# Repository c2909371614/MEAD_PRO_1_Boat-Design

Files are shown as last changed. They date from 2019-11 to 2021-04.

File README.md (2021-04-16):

# MEAD_PRO_1_Boat-Design

机器人学院的MEAD 项目--小船项目分享

<<<<<<< HEAD
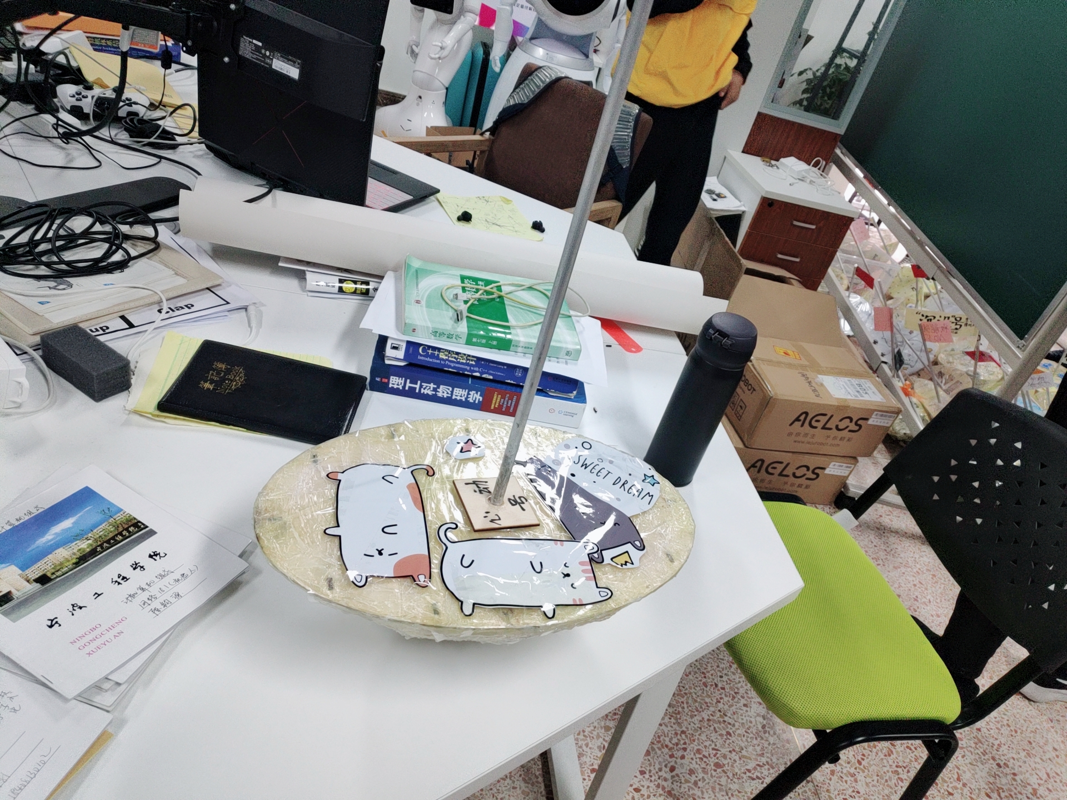
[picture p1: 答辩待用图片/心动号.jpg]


=======

>>>>>>> a22fceb2be759056432b4c75dd355906650863ec
<center> fig 1. 心动号 </center>
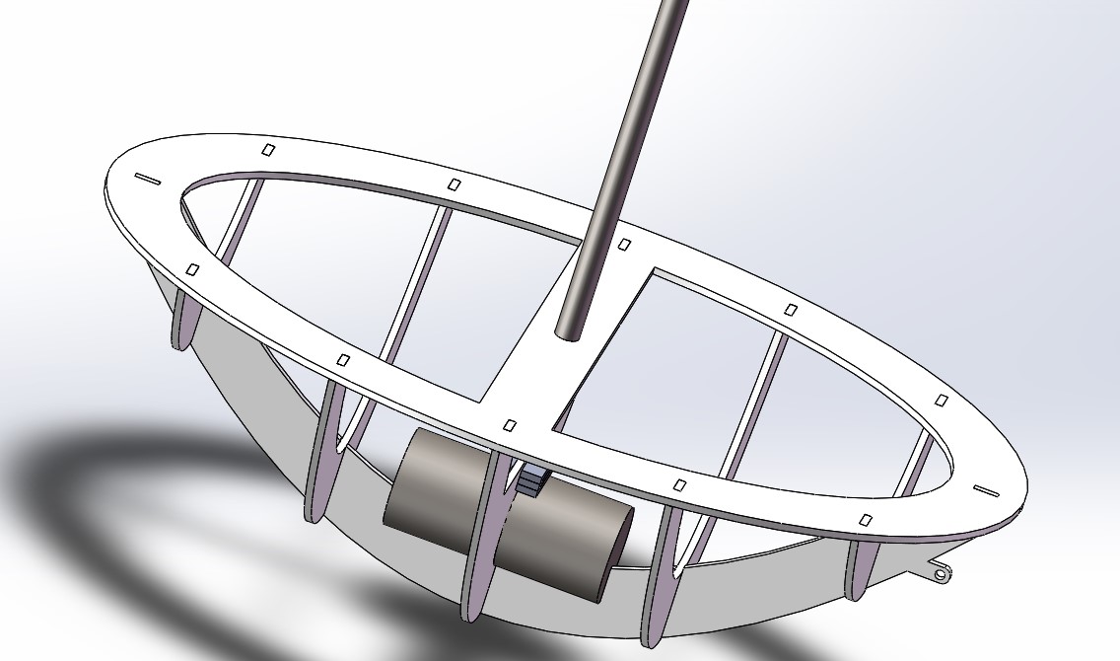
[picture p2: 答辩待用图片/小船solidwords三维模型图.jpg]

<center> fig 2. 小船solidwords三维模型图 </center>
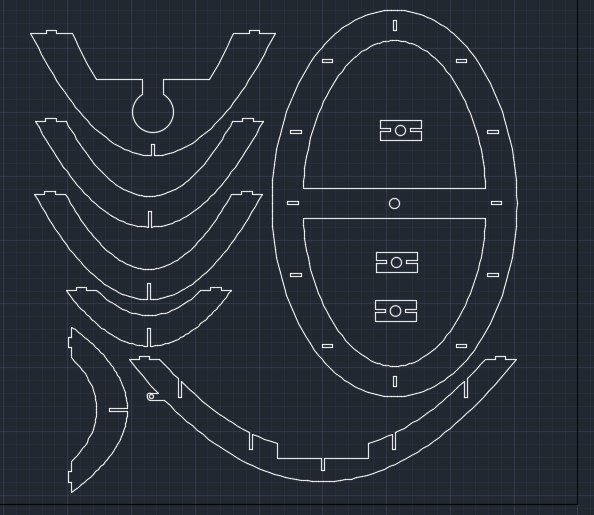
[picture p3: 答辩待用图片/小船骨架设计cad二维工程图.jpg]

<center> fig 3. 小船骨架设计cad二维工程图 </center>

### 一、MADE项目任务书-- 船只设计项目

		Welcome to the MADE project!!! Here, MADE stands for Mathematical Analysis and Design for Engineering. This is a project-based course, which aims at improving the participators’ understanding of mathematics knowledge and engineering analysis. MADE should be able to help the students to develop a thinking mode of applying theoretical analysis and quantitative calculation, and truly understand the role of mathematics in engineering projects. 

		欢迎来到MADE项目课程。在这里，MADE代表着“用于工程的数学分析和设计”。MADE项目力求以实际应用的案例加深参与者对数学知识与分析方法的理解，并逐步建立在工程问题中采用理论分析进行定量计算的思维模式，真正掌握在实际的工程设计中应用数学知识的方法。

		MADE course is supposed to be challenging, comprehensive, and integrate knowledge of various subjects. But please be assured that the task is feasible, and we look forward to seeing you confidently say, ”Yes, I MADE it!!”

		MADE课程在设计时，就力求做到具有挑战性，全面性，并整合各种科目的知识。但请放心，这项任务是可行的。我们期待看到你自信地说：“Yes， I MADE it！”

**MADE Project 1: Boat Design**

此项目要求你设计一艘船，并满足一定的设计要求。要达到这些要求，你必须要完成制作、测试、研究和计算等多项工作。我们希望通过这项课程中对设计与分析等不同方面的练习，你可以在未来更有信心的面对各项技术工作。

要完成这个项目，你需要各类工作，制作各类零件，并完成你的设计工作。最后，你要展示你的作品，并通过答辩。

**项目对你的预期：**

1. 你应该对船舶设计过程进行背景研究。为此你可能需要在互联网上花费相当多的时间。我们建议你整理出一个造船业的术语列表，并且要确保自己不仅理解造船业中的why，还要了解其中的how。这本身是一个巨大的话题。因此，你可能不会成为专家，但应该熟悉关键的思路。你需要理解的术语包括但不限于：倾斜heel，流线trim，船宽beam，稳定消失角AVS，水下表面积，浮力，位移等

2. 你应该做一些估算，以指导和验证你更详细的设计和分析工作。任何你做出的决定，你都应该能够通过一个快速的计算或论证进行支撑。这个计算或论证至少能够表明你的决定在正确的范围内。不要忘记在正式开始建造你的船模之前检查你的最终设计。设计方案是否准确？它看起来是否稳定？

3. 您应该进行详细的分析以支持您的设计选择，并验证您的测量结果。您应该依靠计算支持你的设计方案。我们要超越猜测和检查的方式，需要使用图表，研究不同选项等。

4. 你要建造一艘船，并将其性能与你的理论分析预测的性能进行比较。

**我们期望你能制造出：**

1. 首先，您需要提供一艘船模，并满足下面指定的设计要求。在项目的最后一天，把这艘船带到课堂上。请注意，在此之前绝对不允许对你的船模进行测试

2. 你需要提供可用于分析给定船舶设计的代码。代码规范细节在文件后续中有说明。

3. 您需要提供一份设计报告，通过计算和测量来对你所做的设计选择进行总结和证明。

4. 最后，您需要提供一份修改后的设计报告以及一封给老师的反馈信，说明在答辩以后，为响应教师建议所做的修改。

**最后要达成的目标**

1. 我们将集体做船的测试。想象一个产品展示日

2. 你的团队将与教师一起坐下来审核您的设计报告。教师将为您提供有关如何改进设计报告的具体反馈等。您将有三天时间修改报告以回应这些建议，并在一页信总结相关的改变。

**船只的设计要求**

您将使用激光切割的硬质板框架设计和制造船只，并且利用所提供的材料构件外壳。

**制造要求**

1. 你只能使用一块***600mmX450mm***的一块硬质板；

2. 必须使用公式驱动的CAD模型创建船只，

3. 船必须接受最小质量为700，最大质量为1000克的货物。在将货物固定在船上之前，应该预先接受检查和批准。

4. 船必须是不含**舭龙骨**的单体船设计（即不得使用外延龙骨板或双船体）

5. 船必须包括桅杆。桅杆将是一个0.5米长，直径***10mm***的铝棒。桅杆的整个长度必须垂直延伸在船底之上。（不得延伸到船底之外）

6. 应将孔眼按照所需的拖曳点连接到船体上，以便进行速度测试。

**性能要求**

请记住，在最后一次挑战之前**不得**进行测试。您应该能够根据计算，知道您的船能否符合以下的各项要求。

1. 当船满载时，必须能够漂浮起来;

2. 当船满载漂浮时，船的甲板应平行于水面;

3. 满载船的消失稳定角（AVS）应该是135度，允许有±10度误差;

4. 船应具有至少0.2 N-m的最大恢复力矩；

5. 船体应尽可能利于快速行进。这一点将使用拉力测试来确定：通过连接在螺旋孔眼处的水平线施加0.1牛顿的恒定力来进行。

**专业性要求**

1. 船模的外观应该很专业；

2. 应该用你们的队名适当装饰你的船模；

3. 制造的船应与报告中的船模设计相同。也就是说，不允许测试前临时修改！！

**代码**

你要创建一段程序代码，用于计算给定船舶设计的重要参数。本节内容概述了对代码的要求。请注意，这些要求的编写方式意在引导你逐步增加各项内容。

你的代码应该包含以下内容，

1. 船体形状的数学函数表示。可以使用符号数学或代码来完成，这会创建一组离散的点，来根据函数形式定义曲面。如果您正在进行二维近似，那么您应该能够在答辩中说明此近似的有效性，包括在计算中如何考虑第三个维度； 

2. 船体形状的可视化，以及来自所有三个方向（纵向，横向和吃水线）的切面的显示

3. 计算给定载荷时的位移，和对于给定载荷和船体倾角的相应吃水线；

4. 为你的船体设计计算质心和浮心，以及这些位置如何随着船体倾角的变化而变化;

5. 在特定负载配置下，你的船体设计方案中，绘制复原力矩作为船体倾斜角函数的曲线图。你应该检查这些结果，确保它们与计算出的质心和浮心位置保持互相吻合。

### 二、我完成了什么

根据小船设计要求（见小船设计项目任务书文件）

1、求出小船底部曲面方程及船高

2、求出龙骨方程、截面方程及甲板方程

3、求出重心及小船向x轴倾斜135°（船体封闭）时的浮心及复原力矩

4、求出吃水线

5、画数量关系图

5.1画出重物质量与吃水线关系的曲线图

5.2画出船长、宽、高分别与复原力矩关系的曲线图

5.3 画出重物质量与重心关系的曲线图（曲线图的纵横坐标表示重心坐标，曲线上的点的大小表示质量）

### 三、解决方案概要

> 		针对如何使用一块***600mm x500mm***的木板制造一艘在承载一定质量的重物的情况下能够平稳的漂浮起来切具有稳定消失角(AVS)的方案进行了研究。通过数学曲面公式来简单的表示船体的曲面，通过曲面积分来计算船体体积、吃水线性、船体的浮心和重心，确定浮心、重心之后计算出倾斜一定角度时的复原力矩。通过使倾斜一定角度时船体重心在浮力方向和船体中心线的交点上来确定AVS(135°)。

>  	以小船最低点为坐标原点，垂直垂直向上为Z轴，船头至船尾的连线为Y轴建立直角坐标系以方程为船体底部曲面方程，最终确定A=8.33，B=3.33，计算得船长length为0.379m，宽width为0.240m高height为0.120m，桅杆重心(0,0,0.292)，重物重心(0,0,0.042)，船体重心为(0,0,0.080)。

### 四、详细解答过程请看项目报告书，找不到自己想要的请留言（by a new issue)

### RESULT



<center>图3 船体倾斜135°复原力矩图

已知$COM(0,0,z_m)$，$COB(x_b,0,z_b)$

浮力$F_浮=<tan\theta,0,-1>\lambda$，其中$\lambda=\frac{G_{all}}{tan^2\theta+1}$

复原力臂$r=COM-COB=<0,0,z_m-z_b>$

复原力矩$M_s=r\times F_浮=0$

### 4.吃水线



<center>图4 水平吃水线

已知船体总重量为$m_{all}$，有$m_{all}=\rho g_水 v_排$

吃水线方程为$z=h$

有
$$
\begin{align}v_排=&\iiint_E{dV}\qquad E = \{(x,\ y, \ z) | x_{Mid}\leq x\leq width, \ y_0\leq y \leq0, 0 \leq z \leq z_0 \}\tag{4}\\v_排=&\int_{xMid}^{x_1}\int_{0}^{y_0}\int_{Ax^2+Bx^2}^{h}{xdzdydx}\tag{5}\end{align}
$$

###

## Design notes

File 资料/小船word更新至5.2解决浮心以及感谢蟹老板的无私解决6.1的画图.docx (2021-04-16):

以小船最低点为坐标原点，垂直向上为Z轴，船头至船尾的连线为Y轴建立直角坐标系假设船体底部曲面方程为，船高为，桅杆长度0.5m，质量0.1kg，重物的底面半径0.02m，质量1kg，材料面密度为0.1458kg/m²

求

1、 龙骨方程

x取0，得到z=By²,即为龙骨方程。

2、 任意截面方程

设截面所在平面为ax+by+cz+d=0①

则任意截面方程为①与相交部分，即

（a,b,c,d为任意常数）

3、 甲板方程

甲板面平行于xoy平面，所以令曲面方程中的z=H即可。即

4、假设A=17656，B=14.8，H=0.2

4.1求吃水线深度

先求m总=m船+m甲板+m重物+m桅杆

已知桅杆的质量为0.1kg，重物的质量为1kg

所以m总=m船+m甲板+1.1

已知船的面密度，求得船的表面积即可求得船的总重。所以

由于投影面为，对称性好。可以将积分转化为第一象限积分的四倍。即

所以船体的总表面积为

使用matlab的quad2d函数求解，得到结果为 0.113379476543658m³

再用ρV=m求得m船体= 0.016530727680065kg

最终求得m总=1.116530727680065kg

再使用m=ρ水V排；ρ水=1000kg/m³；求得V排=m*10⁻³,单位m³。

因为甲板平行于水面，所以设吃水线高度为H对浸入水内船体进行体积积分，即求得V排。

通过二分法迭代求H，最终求得H=0.120879583074898m，即吃水线深度。

4.2求重心

根据方程可以知道船体有良好的对称性，关于x轴y轴均对称，即船体的重心的x坐标和y坐标均为0。仅需求z坐标即可。

使用matlab的quad2d函数求解，得到结果为0.003030405142533m。

已知三点P（0，0，0.003030405142533），Q（x1,y1,z1），R(x2,y2,z2)

(P为桅杆重心，Q为重物重心)

三点对应质量为m0=0.016530727680065kg,m1=0.1kg,m2=1kg。所以质心坐标的xyz坐标如下：

质心坐标为，单位均为m。

5.1 将小船向 x 轴倾斜 140°求出吃水线所在平面的方程

方法①：坐标系转换（把船转过去）

方法②：把水转过来。（以船自身为坐标系）

位置是相对的，既然将小船转140°入水，组成船-水的相对位置；也可以将水面转过来140°组成水-船的相对位置。既然如此，水面就是一个平面，即z=tan140°x+k,这个k就是关键，利用水下船体体积*水的密度=船的总重可以求出k值，确定该水面方程，以船自身为坐标系的该水面方程即为吃水线方程。

以下将进行对于方法二的求解：

已知船的坐标方程和吃水线方程，求k。k有三个临界点，分别是

①吃水线与原点相交（水漫得最高，ps:排水体积大于总体积一半肯定够了）

排水体积关于z轴分为两部分，右侧的体积为总体积的一半远大于所需排水体积，左侧未算，但是肯定是大于0的。

②吃水线与船的左上点相交(水漫到的关键点，ps:通过计算漫到这点排水体积还不够一点点)

根据z=tan140°x+k与可以求得k=0.151320293728474；然后求吃水线与船的另一侧的交点的x值，使用联立求解可以求得x=x0=0.049897854853113（我是使用二分迭代的方式求得的）；最后使用积分求其排水体积。此处使用船体总体积减去水上体积更容易计算。船体总体积已经算过了，使用第四题中的结果即可。水上体积表达式如下：

积分出来结果为0.001595895710214m³。

再用船体总体积减去其积分结果，求得水下体积为0.001099084023240m³略小于所需排水体积0.001116530727680m³

③吃水线与船中心的最高点相交(水漫到的最低点，ps:通过计算漫到这点排水体积还是不够)

最终计算结果说明：

由①②③可知，k在k1和k2之间，k1即①中的k=0，k2即②中的k=0.151320293728474;

此时k为变量，通过二分迭代，每次计算k时，分别计算水面与船体的交点的x轴坐标，此时的计算函数其实类似与②中的公式，只需要将x0和这两个上下限，改成由随k而变的xmin和xmax，这两个值也可以利用每次二分迭代k的时候，使用二分迭代求得。最终利用②中的积分和船的总体积求得排水体积。此处只给出结果，k=0.150534414731095。

最终那个吃水线方程为z=tan140°x+0.150534414731095。

5.2 将小船向 x 轴倾斜 140°，求浮心及复原力矩

浮心：

已知水下船体关于y轴对称，对称区域也关于y轴对称，所以关于y的奇函数的积分为0。根据浮心定义：浮心就是被排开的流体的重心。所以可以利用重心公式求解。

设其坐标为，已知y0=0。仅需求x0和z0即可。

已知吃水线方程为，k为已知常数（0.150534414731095）。所以可以根据吃水线平面和船体的交线求得两端交点x1，x2，此处由5.1二分迭代求k的过程中已求出，分别为-0.057953430474795和0.049815920068628。然后将积分区域分成三片，左边右边两块和中间一块。三块y的上下限均在之间；左右两块z的上下限分别为H和曲面方程，中间一块z的上下限分别为H和吃水线平面方程；而三块x的范围，以x1，x2分割，左边的在与x1之间，中间的在x1，x2之间，右边的在x2和之间。最终按重心三重积分求结果。以下为公式：

;

关于x：

右边的积分同理可得，只要将上下限换掉即可。

将三者积分相加，除以m得最终浮心的x坐标，约为0.013938450731625，单位m。

关于z：

右边的积分同理可得，只要将上下限换掉即可。

将三者积分相加，除以m得最终浮心的z坐标，约为0.170003799370430，单位m。

复原力矩：

复原力矩

6.1 画出重物质量与吃水线的曲线图

①4.1船的重量公式算出船的总重，再根据V排=总重量

求出对应的吃水线H，再用程序求出每次增重1g对应的吃水线。画图

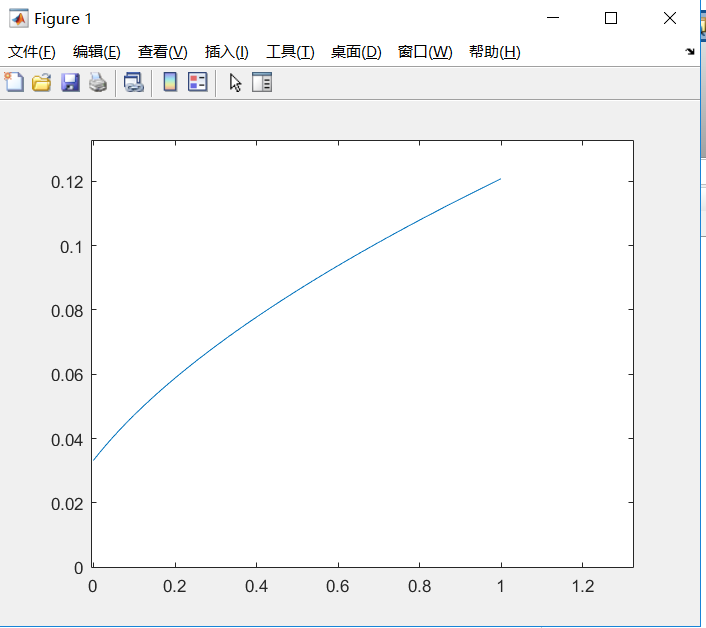
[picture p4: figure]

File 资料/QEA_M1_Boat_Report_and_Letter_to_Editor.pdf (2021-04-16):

# Designing the Steggie

Kyle Combes & Alex Core

Abstract—This report will detail the necessary background information of boat making through mathematical functions, explain specific design decisions and reasoning behind these choices, elaborate on the various calculations involved in this process, and discuss the real world performance of the boat. The performance qualifications of this project were to design a boat that floats in water, has a parallel deck to the surface of the water. The angle of vanishing stability is between 120◦

and 140◦
,
has a maximum computer righting moment of at least

### 0.2 Newton-meters, and is as fast as possible under a

constant force of .1 Newtons. The boat will be made out of hardboard and vinyl, and will contain a mast and eyelet. The project required a understanding of the background and terminology involved to make proper calculations using Mathematica. This use of mathematica was only possible with a understanding of the basics of multivariable calculus and the physics ideas of center of mass, center of buoyancy, and torque. The design was started as simple and was adjusted to the needs of the Mathematica calculations and utilized to find equations that define the boat. These equations were then exported to Solidworks. The parts of the boat were laser cut out of hardboard and then glued together and wrapped and vinyl. The boat was then tested for the above requirements.

I. BACKGROUND AND TERMINOLOGY

To understand the boat, a basic foray into the terminology and ideas behind boats and boat building was necessary. One such area needing exploration was the parts of the boat. The hull is the main body of the ship of the vessel including the bottom, sides, and deck. The bow it the forward part of the hull of the ship or boat it is a necessary proponent to drag. The stern in contrast is the after most part of the hull. The deck is an important part of the design and is the topmost portion of the boat. Where the hull meets the water is the waterline, which is essential to calculations. The buttock is the lines formed at a point of intercepts between the centerline plane and the sheer plane. A section is a division of a boat on a plane. The heel angle is the amount the vessel is tilted from upright. Center of mass (COM) is a point representing the mean position of matter. Physics calculations can be focused on that one point. The center of buoyancy(COB) is the centroid of the submerged part of the boat. This can thought of as the center of mass of the displaced water for simplicity. One facet of this project is the angle of vanishing stability (AVS). The AVS is the heel angle at which the the boat is between capsizing and self righting. It can barely balance due to the center of mass and center of buoyancy being at a equilibrium. The righting moment is the is the restoring force of the torque which is created by the center of mass and center of buoyancy to self right when the heel angle is above the AVS.

II. DESIGN CONSIDERATIONS

A. Units and Conventions
All of our units were in inches and grams, and we used a right-hand, 3D coordinate system with the origin at the center of the bottom of the hull. The x-axis ran port to starboard, with starboard being positive, and divided the boat in half. The y-axis ran lengthwise, also dividing the boat in half, with the bow in the positive direction. The positive z-axis extended skyward. (See Figure 1.)

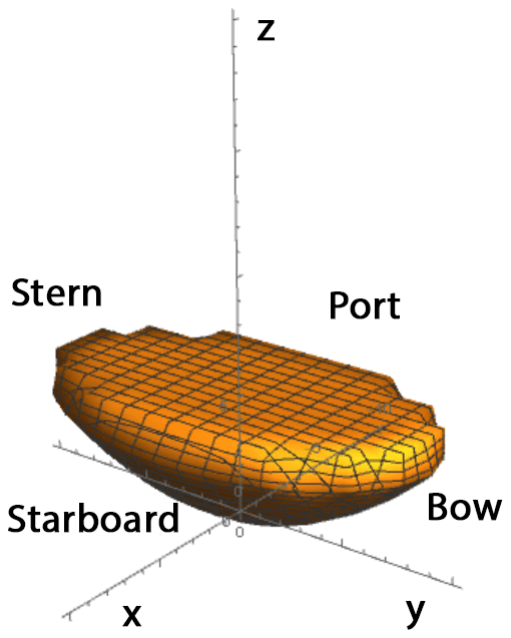
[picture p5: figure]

Fig. 1: Our coordinate system was defined with the x-axis running from port to starboard, the y-axis running lengthwise, and the z-axis extending vertically.

In order to simplify our calculations, we decided to model a rotating waterline rather than a rotating boat. As such, the forces of gravity and buoyancy rotated with the water. θ represented the angle of rotation of the waterline, with positive being a counter-clockwise rotation about the y-axis.

B. Making a Floating Boat
The first step in designing a boat is to make sure it’s going to float. Generally speaking, when an object floats in water, the buoyant force pushing back up on that object is equal and opposite to the force pushing the object down in the water. With a boat, the downward force is the force due to gravity (Figure 2). Therefore, for a buoyant boat:
F~B = −F~Gboat | (1)

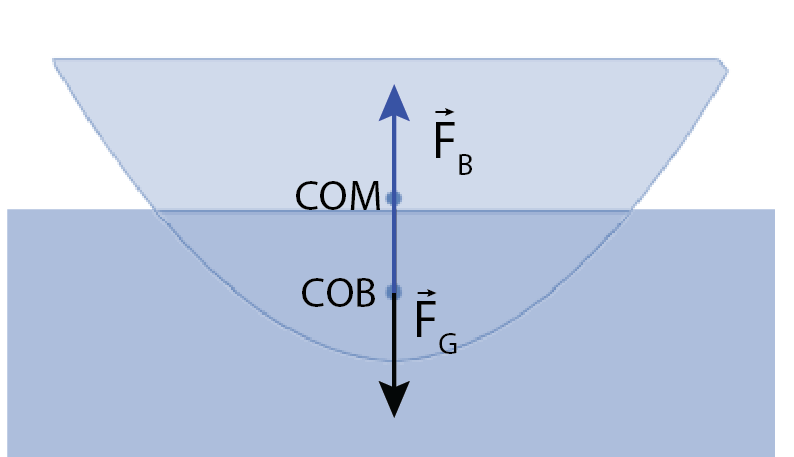
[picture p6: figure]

Fig. 2: When a boat is floating, the buoyant force is equal and opposite the force due to gravity acting on the boat.

Additionally, the buoyant force is equal to the mass of the water displaced multiplied by the acceleration due to gravity.

F~B = mwaterg | (2)

Since the mass of water is equal to its volume times its density, we can also write:

F~B = ρwaterVwater~g | (3)

That means that in order for our boat to float, the boat must have suitable density and displace enough water such that the buoyant force can counteract the force of gravity.

C. Finding the Waterline
The buoyancy concept can be extended to find the waterline on the submerged vessel. If the floating boat has a mass, mboat, then the water it displaces must also have the same mass:
mboat = mwaterdisplaced | (4)

The mass of the boat can be calculated by integrating all of the point masses in the region defined by the boat. Similarly, the mass of the displaced water can be found by taking the volume of the submerged region of the boat (found by integration) and multiplying it by the density of water. (One must remember to take into account the fact that the waterline is rotated when defining the submerged region.) Combining these two concepts allows us to rewrite the above equation as follows:
Z Z

~r∈Boat

ρboatd~r =

Z Z

~r∈Submerged

ρwaterd~r (5)

Solving for the upper bound on the submerged region will give you the waterline.

D. Making it Sit Flat
In order to meet the second requirement, it is necessary to design the boat such that the COM and COB are aligned along the x- and y-axes when the plane of the deck is parallel to the plane of the water. Otherwise, a torque will result about the COM, as illustrated for the x-axis in Figure 3.

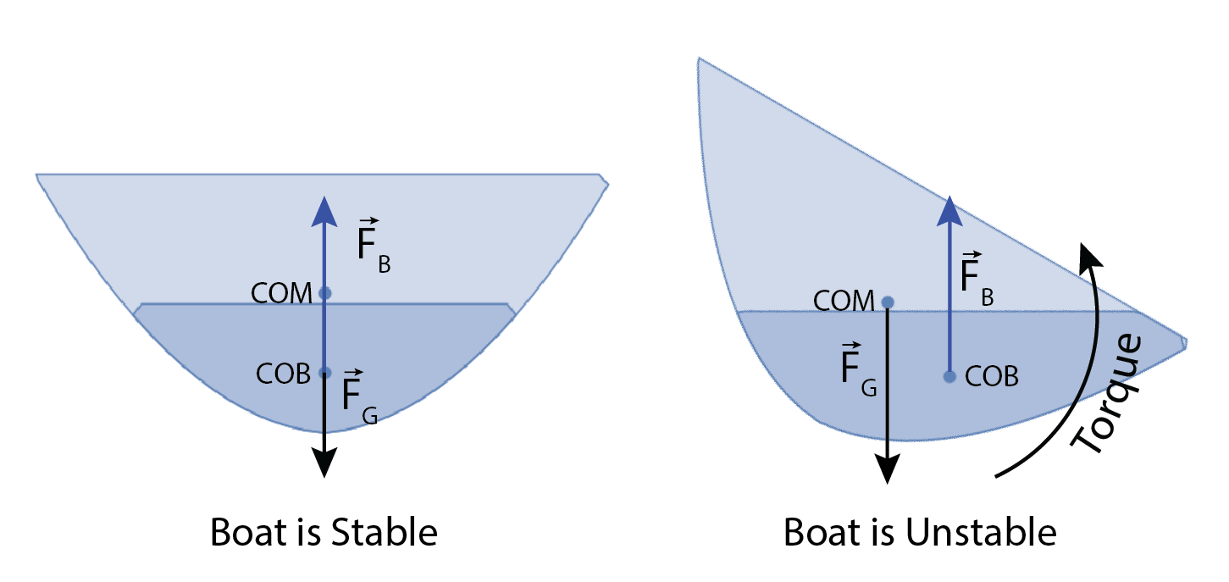
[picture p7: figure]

Fig. 3: Unless the COM and COB are aligned vertically, there will be a torque about the COM and the boat will rotate.

E. Determining the Angle of Vanishing Stability
In a well designed boat, heeling the boat (θ 6= 0) will result in the COB moving out from under the COM in the direction the boat is leaning. This will provide a stabilizing torque, which will right the boat (Figure 4 center). In a poorly designed boat, such as one that is too narrow (Figure 4 right), the COB moves in the opposite direction and provides a destabilizing torque, causing the boat to capsize.

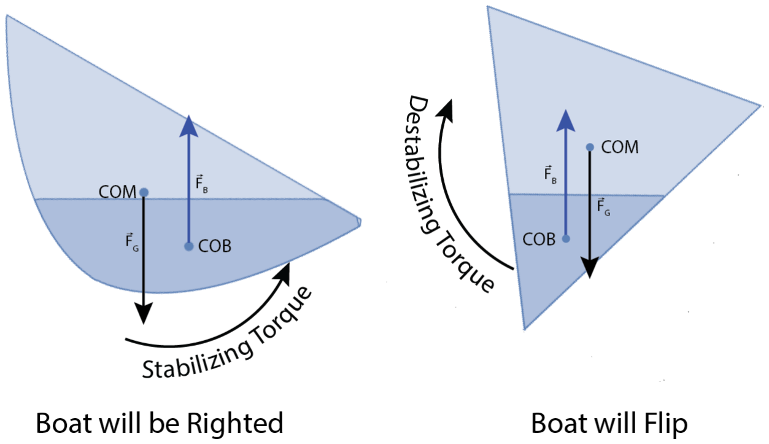
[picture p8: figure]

Fig. 4: The stability of a boat depends on the relative locations of the COM and COB. In order for a boat to sit flat (left), the COM and COB must be aligned in the horizontal axis. In a well designed boat (center), the COB moves in the direction the boat is leaning, and the buoyant force rights the boat. In a poorly designed boat (right), the COB moves in the opposite direction, and the buoyant force flips the boat.

To achieve the desired angle of vanishing stability (AVS), the boat should be designed such that the relation of the COM and COB shifts from the middle scenario to the right scenario at that value for θ.
1) Finding the Center of Mass: To determine the torque acting on the boat at a given heel angle, we first need to calculate the COM and COB. To calculate the COM in R3, one can use the double integral

~rCOM =

1

Mboat Z Z

~r∈Boat

ρ~r d~r | (6)

Since Mboat can be found by integrating all of the point masses in the region, the above equation can be rewritten as follows:

~rCOM =

RR

~r∈Boat

ρboat~r d~r

RR

~r∈Boat

ρboat d~r | (7)
2) Finding the Center of Buoyancy: In order to find the COB, which is where we assume the buoyant force to be acting, one needs to find the centroid of the submerged region of the boat. If ~r ∈ Submerged is the region bound by the water (as determined in Section II-C) and the boat, then the centroid can be computed using the following integral:

~rCOB =

1

Vboat Z Z

~r∈Submerged

~r d~r | (8)

Since Vboat can be found by integrating the submerged region, the above equation can be rewritten as follows:

~rCOB =

RR

~r∈Submerged

~r d~r

RR

~r∈Submerged

d~r | (9)

Once the COB and COM have been determined, one needs to calculate the moment arm, which is the position vector of the COB relative to the COM. This can be calculated like so:

~rmomentarm = ~rCOB − ~rCOM | (10)
3) Calculating the Buoyant Force: When calculating the buoyant force, one must remember to account for the rotated waterline (as illustrated in Figure 5). Given that the buoyant force is equal and opposite the force of gravity and that θ represents the angle of rotation of the waterline, the components of the buoyant force acting on the heeled boat (Figure 5) can be found like so:

F~Bx = −|F~G|sin(θ)

F~By = |F~G|cos(θ)

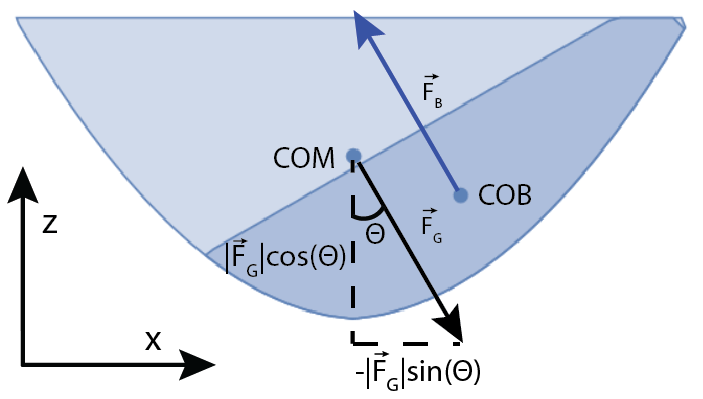
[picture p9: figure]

Fig. 5: When considering the buoyant force, it is important to remember it does not point directly in the positive z direction, due to the rotated waterline.

4) Determining the Moment and the AVS: With the moment arm and buoyant force vectors calculated, it’s a simple enough task of calculating the resulting torque. All one has to do is cross the two vectors:
~τ = ~rmomentarm × F~B | (11)

Performing the calculation for a variety of heel angles, plotting the results, and checking where the moment is zero will reveal the AVS. (The result for our boat can be seen in Figure 9.)

III. PROPOSED DESIGN AND JUSTIFICATION
We initially toyed with the idea of a hull shape with a concave region, like that shown in Figure 6. However, we ran into stability problems due to the COB shifting in the wrong direction at low heel angles.

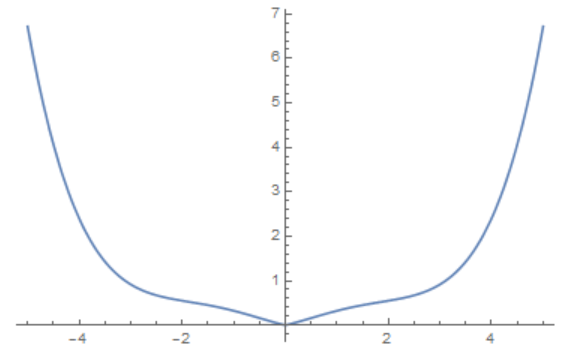
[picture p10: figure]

Fig. 6: Our original hull shape with concavity. We were forced to abandon this design due to stability issues.

In an attempt to fix our stability problems, we switched to a parabolic hull shape. We tweaked the coefficients on |x| and x

2 with the goal of designing a stable boat with the narrowest hull possible, but we were unable to fully optimize the shape due to time constraints and issues with our Mathematica code. We ended up settling on a ”good-enough” hull definition and chose a coefficient for y

2
that would make our boat about 20 inches long. In the end, our hull declaration could be described by z = 0.14(0.53|x| + x

2
) + 0.0528y

2
Bounding this on the top with our deck equation of z = 5.2, we ended up with the following inequality to define our boat (B) in R3:

B = 0.14(0.53|x| + x

2
) + 0.0528y

2 ≤ z ≤ 5.2 (12)

A section, buttock, and deck view can be seen in Figure 7:

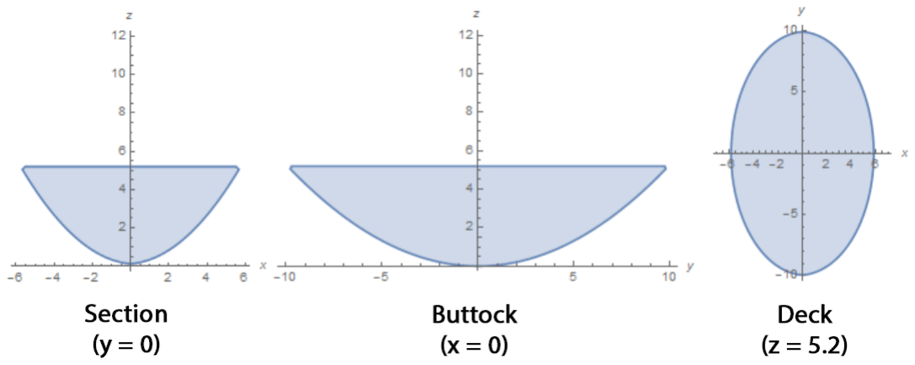
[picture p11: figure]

Fig. 7: Views of the hull and deck from various angles.

This inequality made our boat symmetric about the xand y-axes, which meant our COM along those axes was zero:

~rCOMx = 0
~rCOMy = 0

(13)

In order to find the COM along the z-axis, we needed to calculate the COM for the mast, ballast, hull sections, deck, and structural keel separately and combining the result. First we had to find the weighted sum of the mass of the hull sections, where each hull section was at one of the y positions in the set H:

H = {−8, −6.75, −4.5, −2.25, 2.25, 4.5, 6.75, 8} (14)

To do that, we summed up the points in each region multiplied by their displacement (z) and the density of fiberboard (ρf ):

Wsections =

X

y∈H

Z Z

B

ρf z dzdx | (15)

Once we had the mass of the hull sections, we added that to the weighted mass sum of the structural keel, ballast, and deck, which was computed using a similar method. The resulting sum can be called Sweighted. Furthermore, if Mboat is the mass of the entire boat, then we can find the COM by doing the following:

~rCOMz =

Sweighted Mboat | (16)

After running a few simulations, shifting our ballast up and down, and looking at our stability curve (Figure 9), we realized we would need to make the COM as low as possible to get an AVS above 120◦
. (A different hull

equation may have fared us better, but we didn’t have time to redesign the hull entirely.) Thus, we used eight solid hull sections, cut out a significant portion of the deck, and placed our 990g of ballast at the lowest point possible in our hull. Figure 8 shows a 3D CAD rendering of our boat skeleton.

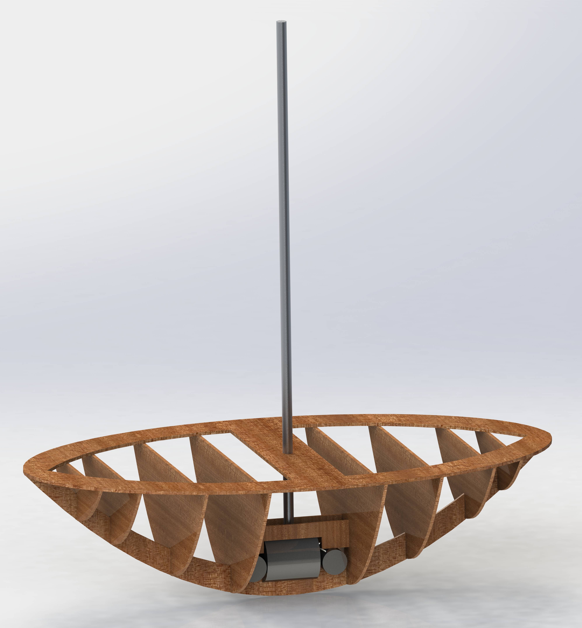
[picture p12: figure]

Fig. 8: A rendering of our CAD boat model. Solid hull sections and a cut-out deck, combined with situating the ballast at the bottom of the hull, gave us the lowest COM.

Using a Mathematica model, we were able to predict the stability curve and AVS shown in Figure 9.

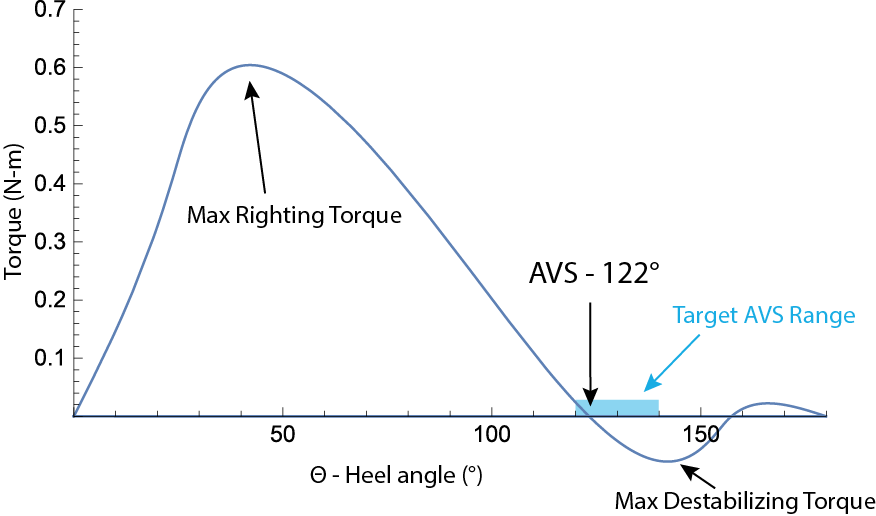
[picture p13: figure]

Fig. 9: Plotting the resulting torque on the boat at various heel angles revealed our AVS to be about 122◦

IV. PERFORMANCE

During the test the boat was successfully able to float flat. It was completely airtight and had no leakage or issues. In addition, our AVS was 122◦
, which was
exactly as our Mathematica model predicted (within measurement error). The final portion of this project was the drag test. Under 0.1 Newtons of force the vessel’s speed was 0.401 m/s. Overall the boat performed exceedingly well.
V. CONCLUSION
The boat had a variety of successes and failures over the course of its development. In the end, she met all the design requirements and performed according to our calculations. She also looked beautiful on snow (Figure 10). Going forward with this subsequent improvements would be to increase the speed of the boat. Although the speed of 0.401 m/s is respectable, there are many different boat designs and shapes that outclass Steggie in this regard. Further research would need to be done towards speed based boat designs to augment the current design while continuing to meet the other requirements. As shown below the final project was assembled with lots of care as to fall in line with the calculations.

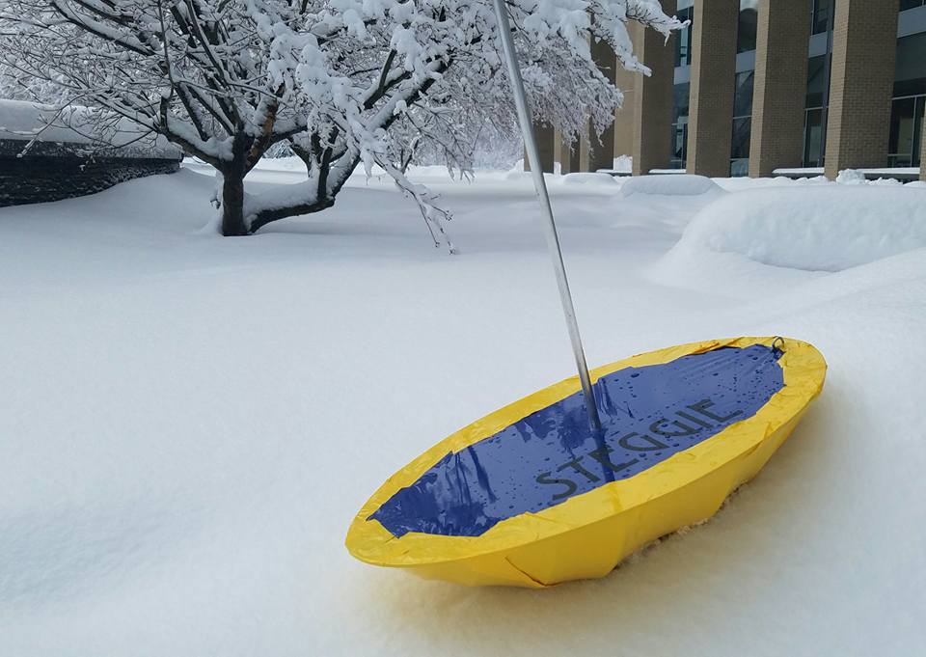
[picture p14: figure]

Fig. 10: Steggie showcased in the fresh snow.

## Alexander Core & Kyle Combes Quantitative Engineering Analysis Students QEA Module II February 23, 2017 Rebecca Christianson Quantitative Engineering Analysis Instructor

Dear Editor,

## We have addressed your concerns regarding our report. Here is a summary, broken up according to affected section:

In our abstract, we changed it so it became much more descriptive and actually detailed the entire project. Another big change was the boat requirements no longer being bullet pointed.

In our section titled “Background and Terminology,” we defined center of mass and center of buoyancy so they could be utilized to explain the angle of vanishing stability.

In our section titled “Design Considerations,” we corrected our equations so that every vector is correctly denoted by an arrow. All annotated vectors in figures had arrow hats added as well. We also reworded the sentence in Section II-C which previously stated incorrectly that gravity was always acting in the negative z direction. Now it correctly states it rotates with the waterline. We also added a reminder to remember the rotated waterline in Section II-C and two further mentions of the angle of rotation, Ө, in Section II-E.

In our section titled “Proposed Design and Justification,” we added discussion on the process of settling on our particular hull shape. We also added details, including equations, on our center of mass calculation for our boat design.

In our section titled “Conclusion” we added a short sentence to tie in our picture.

We look forward to hearing your feedback on our revised edition.

Thank you for your time,

## Alex Core and Kyle Combes

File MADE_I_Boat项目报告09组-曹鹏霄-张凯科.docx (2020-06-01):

宁波工程学院

机器人学院

MADE项目I小船项目报告

专业、班级 网络工程(机器人)、18-1班

姓名 曹鹏霄 学号 18401190120

姓名 张凯科 学号 18402050209

日期 2019年11月10日

指导老师 张浩向

MADE项目I小船项目

曹鹏霄¹，张凯科²

摘要：针对如何使用一块600mm x500mm的木板制造一艘在承载一定质量的重物的情况下能够平稳的漂浮起来切具有稳定消失角(AVS)的方案进行了研究。通过数学曲面公式来简单的表示船体的曲面，通过曲面积分来计算船体体积、吃水线性、船体的浮心和重心，确定浮心、重心之后计算出倾斜一定角度时的复原力矩。通过使倾斜一定角度时船体重心在浮力方向和船体中心线的交点上来确定AVS(135°)。

以小船最低点为坐标原点，垂直垂直向上为Z轴，船头至船尾的连线为Y轴建立直角坐标系以方程为船体底部曲面方程，最终确定A=8.33，B=3.33，计算得船长length为0.379m，宽width为0.240m高height为0.120m，桅杆重心(0,0,0.292)，重物重心(0,0,0.042)，船体重心为(0,0,0.080)。

关键字：木板；小船；复原力矩；AVS；曲面积分；吃水线；浮心；重心；

Abstract: This paper studies how to use a 600mm x 500mm board to make a vessel which can float smoothly and have a stable vanishing angle (AVS) under the condition of carrying a certain weight. The curved surface of the hull is simply represented by mathematical curved surface formula, and the hull volume, draught linearity, buoyancy center and center of gravity are calculated by curved area division. After the buoyancy center and center of gravity are determined, the restoring moment at a certain angle is calculated. The AVS (135 °) is determined by making the center of gravity of the hull at the intersection of the buoyancy direction and the hull centerline at a certain angle.

Taking the lowest point of the boat as the coordinate origin, the vertical vertical upward as the z-axis, and the line from the bow to the stern as the y-axis, the rectangular coordinate system was established, and the equation was taken as the curved surface equation of the bottom of the boat. Finally, a = 8.33, B = 3.33 was determined. The length of the ship was 0.379m, the width of the ship was 0.240m, the H eight of the ship was 0.120m, the center of gravity of the mast (0,0.292), the center of gravity of the heavy object (0,0.042), and the center of gravity of the ship was (0,0.080).

Keywords: plank; boat; restoring moment; AVS; surface integral; waterline; center of buoyancy; center of gravity;

# 1.小船设计简介

机器人学院第一个MEAD项目小船项目作为机器人学院大二学生的其中考核项目旨在锻炼学生的运用数理知识和计算机相关软件来解决实际问题的能力。小船模型的设计要求理解重心、浮心、复原力矩、AVS、船舶稳性的概念。需要确定小船的长宽高的比例，它们在一定程度上决定着你小船大部分的性能。其中数学的曲面积分、物理的力矩知识将是项目的最大挑战。

# 2.符号的定义

表(3-1)符号说明

符号 | 说明
| 桅杆质量
| 重物质量
| 船体质量
| 船高
| 水面与船体曲面正半轴交点
| 水面与船体曲面负半轴交点
| 水面与船体甲板交点
| 水平吃水线高度
| 复原力矩
| 复原力臂

# 3. 小船设计方法和理由

# 3.1设计概述

首先以小船最低点为坐标原点，垂直垂直向上为Z轴，船头至船尾的连线为Y轴建立直角坐标系。之后通过经验确定小船的曲面方程模型和小船的长宽高，进而计算出曲面方程的参数。计算出小船的甲板方程和倾斜各个角度的水面方程，从而确定了各倾斜角度的计算体积和重心时的积分上下限。计算出135°时的浮心坐标，将浮力方向与Z轴坐标的交点定为的船体的整体重心坐标，如此便可将小船AVS确定为135°。计算出纯船体的重心坐标通过组合体重心公式来确定桅杆和重物的坐标。

# 3.2小船曲面方程的确定

通过对船舶资料的阅读和现实中船舶的形状来选择小船底部的曲面方程。绘制出的曲面图，如图(3-1)，发现与船体形状十分相像决定使用作为船体的曲面方程。

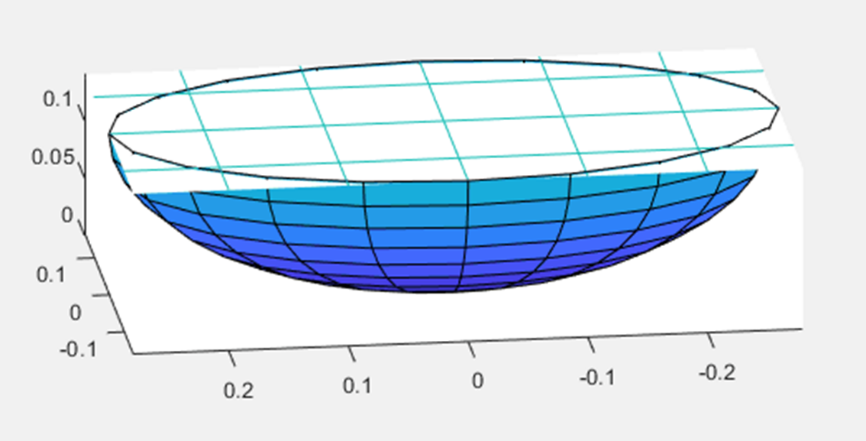
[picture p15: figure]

据经验确定长宽比值为1.58，高宽比值为1，船高H确定为0.12m。

图(3-1) 的曲面图

# 3.3龙骨和甲板的确定

船舶龙骨是在船体的基底中央连接船首柱和船尾柱的一个纵向构件，它位于船的底部。通过对龙骨方程的计算即可确定船体龙骨。令船体曲面方程中的即可获得龙骨方程

(3-1）

从而确定龙骨大小。

甲板是船体的重要构件，是船舶结构中，位于内底板以上的平面结构，用于封盖船内空间而我们小船模型中的甲板位于船体最上方。对于甲板的确定也可同确定龙骨大小一样计算甲板的方程。令可以获得甲板方程

(3-2)

# 3.4 倾斜不同角度水面方程的确定

# 3.4.1整体关系式的确定

当小船浸入水中时根据阿基米德浮力定律有

(3-3)

其中

# 3.4.2积分方程区域的确定

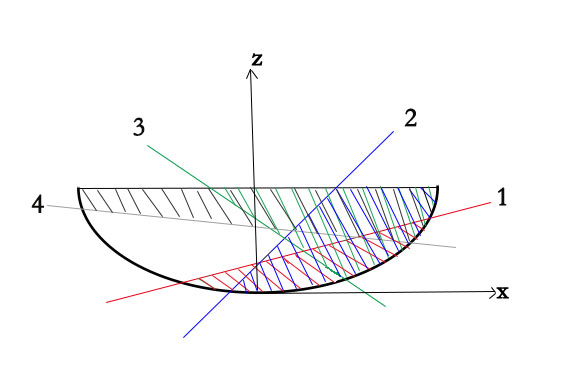
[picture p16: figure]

当小船倾斜不同角度时x，y，z的积分上下限确定方程不同，可以分为4种情况，如图(3-2）

图（3-2）四种不同情况下的水面方程

定义水面方程与船底曲面相交于轴正半轴的坐标为，交负半轴坐标为，交甲板方程为，水面方程为，。

船体无倾斜时

中的其中为吃水线高度，，确定，其中为水面方程，此时，

船体倾斜时

假设水面方程过甲板最右端点时的角度为，过左端点时的角度为。则水面可有分为以下四种情况：

（1）

：

由于此时小船排开水的体积积分区域的y的范围会随着水面方程的改变而改变不方便计算，我们可以积分计算出船体水上体积，再通过总体积减去船体水上体积即可得船体排开水的体积。

(3-4）

图 (3-3) 时水面与船体xoz平面图

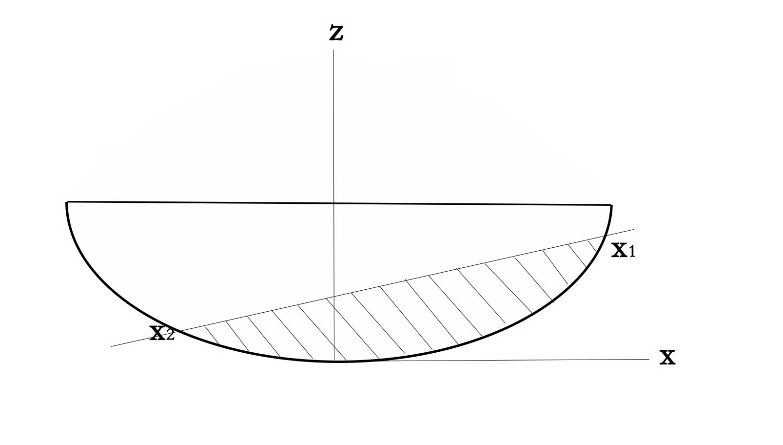
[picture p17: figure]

（2）

：

此时和a相同y的积分区域不好确定我们可以通过总体积来减去船体水上体积来得到

(3-5）

图 (3-4) 时水面与船体xoz平面图

（3）

：

时z轴的积分上限为H所以y的上限不会受到z轴坐标的影响直接计算比较方便计算

(3-6)

图 (3-5) 时水面与船体xoz平面图

（4）

：

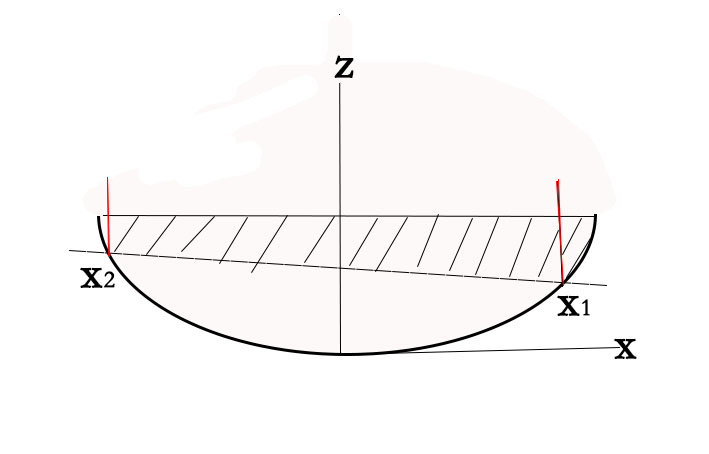
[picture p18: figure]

此时z轴的积分上限为H所以y的上限不会受到z轴坐标的影响直接计算比较方便计算

图 (3-6) 时水面与船体xoz平面图

(3-7)

# 3.4.3记忆化区间二分查找确定水面方程系数

通过记忆化的区间二分查找可以确定水面方程在不同倾斜角度下，的值。

当遇到方程无法直接求解的情况下，可以通过程序迭代来试符合要求的方程解。一般迭代算法可以使用梯度下降法来迭代，但是梯度下降法的时间复杂度是的，再加上matlab的内置积分函数耗时也是十分大的，如果使用这种方法甚至会导致计算一个倾斜角度的水面方程需要花费10分钟，这是无法接受。而可以发现函数是一个单调递增的，这就可以使用二分查找的方法来优化迭代算法，二分查找的时间复杂度是，这样计算一个角度可以缩短到1分钟以内。但是这还是不够快。经过观察发现当船体的倾斜角度增大，x的区间也是在单调变化的。所以我们可以利用上一次的x的区间值来缩减二分查找的区间范围，这样平均能提高3倍的运算速度，具体根据数据的分布不同会有不同的差别。

# 3.5吃水线的计算

当小船浸入水中时根据阿基米德浮力定律有其中有

(3-8)

# 3.6浮心和重心的计算

# 3.6.1浮心(COB)

在确定了水面方程和排开水的积分区域之后计算浮心会十分便捷。假设浮心有

(3-9)

积分区域E在3.4.2积分方程区域的确定已经计算完毕。

无法直接进行积分的需要使用组合体重心计算公式来进行推算

(3-10）

# 3.6.2重心(COM)

要使AVS等于135°，需要使复原力矩等于零，根据公式要使重心在浮力的作用线上。首先计算出其浮心。已知水面方程。假设重心根据便可得

(3-10）

3.7数量关系图的绘制

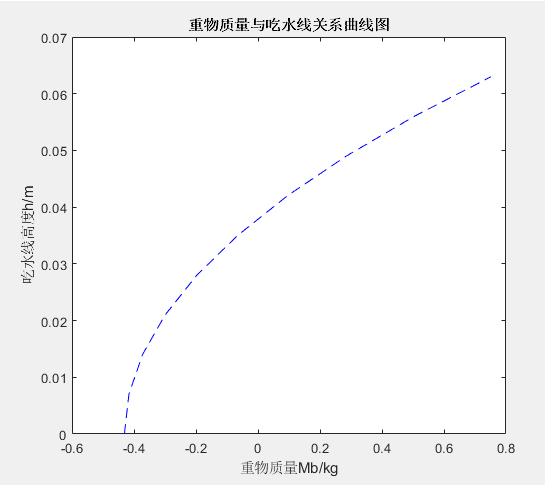
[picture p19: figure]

3.7.1重物质量与吃水线关系的曲线图

图 (3-6) 重物质量与吃水线关系的曲线图

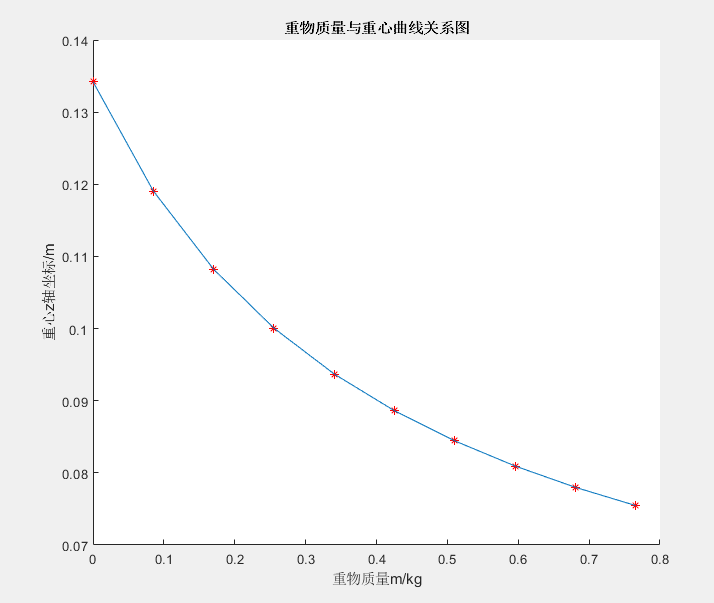
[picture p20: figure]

3.7.2重物质量与重心关系的曲线图

图 (3-7) 重物质量与重心关系的曲线图

# 4.制作方案

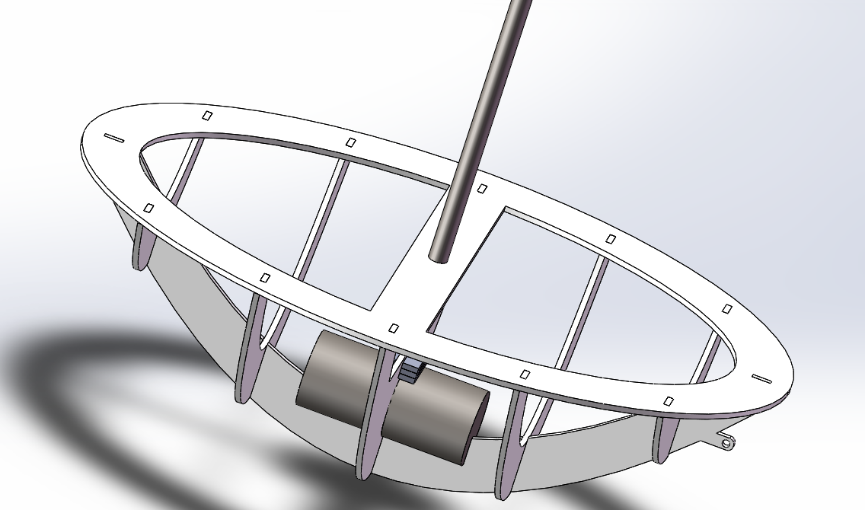
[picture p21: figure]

经过计算确定了小船的长宽高之后通过solidwords绘制小船骨架的三维模型，再将三维模型转成cad可读的二维工程图，最后通过激光从木板中切割出骨架零件进行拼装。

图 （4-1）小船solidwords三维模型图

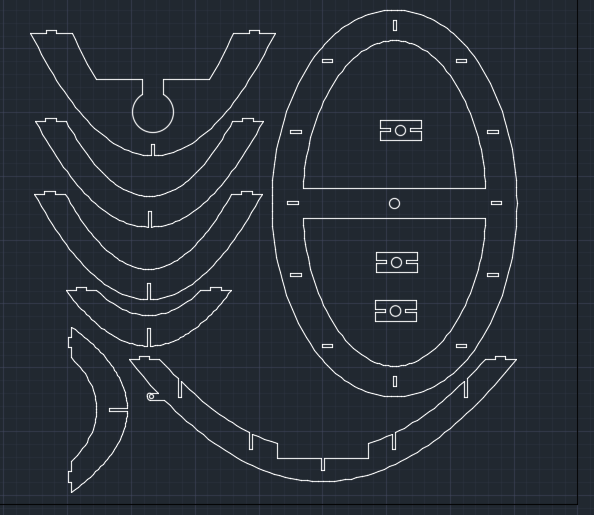
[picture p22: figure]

图 （4-2）小船CAD二维工程图

# 5.比较性能

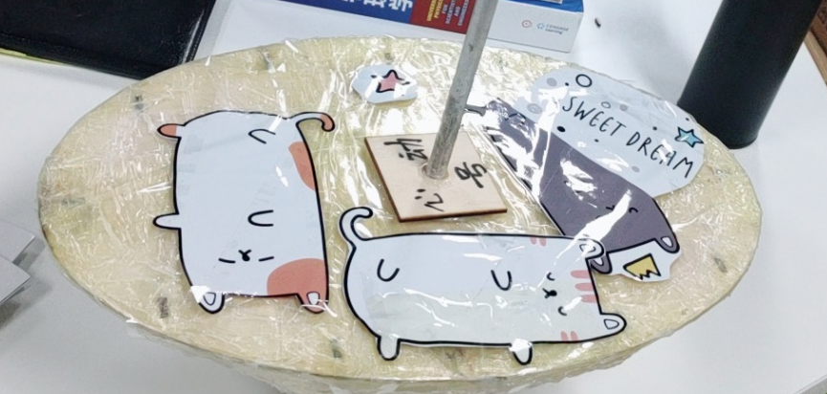
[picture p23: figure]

图 （4-3）小船实体图

理论性能：AVS为135°

实际性能：AVS为125°

意义：理论计算和实际测试一定会有所差别，在计算的过程中应该考虑到理论与实际的误差尽可能的减小这种误差。设计方案和计算应该有一定的容错性。

# 6.结论

小船项目最重要的一部分便是对于多重积分的理解和掌握还有能够使用程序辅助自己进行计算。在积分过程中最难点便是如何去确定小船体积和浮心的积分区域。在此，我们将其积分区域的确定按照交点位置的不同分成了4种情况分别计算，直接积分计算有难度的使用间接法来简化计算。

这次的小船并没有考虑小船的速度性能，想要将小船的行驶速度提高就绝对不能向我们这次一样用简单的曲面进行确定船体形状，最好把船头部分进行分段优化减小船体行进时受到的阻力。

# 参考文献

[1] Kyle Combes:Boat hull design.(2015). http://portfolio.kylecombes.com/

[2] 524890689: 船舶稳性教案.百度文库(2015-04-25).

[3] 李子富，杨盐生，杜嘉立.静水中船舶大倾角横摇稳性的理论计算方法．《 大连海事大学学报 》 ， （2004）

# 附录

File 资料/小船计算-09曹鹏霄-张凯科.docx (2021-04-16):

# 小船计算

指导老师：张浩向 组号：09 组员：曹鹏霄、张凯科

小船最低点为坐标原点，垂直向上为Z轴，船头至船尾的连线为Y轴建立直角坐标系假设船体底部曲面方程为，船高为，桅杆长度0.5m，质量0.1kg，重物的底面半径0.02m，质量1kg，材料面密度为0.1458kg/m²

求

1、 求龙骨方程

龙骨方程为小船底部曲线所以取x=0时即得龙骨方程

2、 任意截面

取任意平面

将小船底部曲线方程与之联立即可得其截面方程

即

取平面x=0则截面方程为所在的平面

3、 甲板方程

甲板高度为H，且小船底部曲面方程为，令可得则该方程围成的区域为甲板区域

4、 假设A=17656，B=14.8，H=0.2A
(1) 求吃水线

根据可求得的大小

其中

其中为为吃水线深度

令为面密度则

有

其中

有

其中积分区域

则

通过matlab的quad2d函数求得

则有

将设两个初始值在此区间对方程进行二分迭代求解出吃水线的深度大约为0.1209m

(2) 求重心

由船底的曲面方程可知船体高度对称所以已知其中心在上求可以在船体体积上对面密度进行积分并对z加权除于m

其中

确定桅杆和重物的坐标

5、

(1) 将小船向 x 轴倾斜 140°求出吃水线所在平面的方程

思路：把水转过来。（以船自身为坐标系）

位置是相对的，既然将小船转140°入水，组成船-水的相对位置；也可以将水面转过来140°组成水-船的相对位置。既然如此，水面就是一个平面，即,需要求出k值利用水下船体体积*水的密度=船的总重可以求出k值，确定该水面方程，以船自身为坐标系的该水面方程即为吃水线方程。

求解：

已知船的坐标方程和吃水线方程，求k。k有三个临界点，分别是

a.吃水线与原点相交，假设水漫得最高排水体积关于z轴分为两部分，右侧的体积为总体积的一半远大于所需排水体积，左侧未算，但是肯定是大于0的。

b.吃水线与船的左上点相交

根据与可以求得然后求吃水线与船的另一侧的交点的x值，使用联立求解可以求得x=x0=0.049897854853113；最后使用积分求其排水体积。此处使用船体总体积减去水上体积更容易计算。船体总体积已经算过了，使用第四题中的结果即可。水上体积表达式如下：

积分出来结果为0.0015959m³。

再用船体总体积减去其积分结果，求得水下体积为0.001099m³略小于所需排水体积0.0011165m³

c.吃水线与船中心的最高点相交(水漫到的最低点

最终计算结果说明：

由a,b,c可知，k在k1和k2之间，k1即a中的k=0，k2即b中的k=0.1513203;

此时k为变量，通过二分迭代，每次计算k时，分别计算水面与船体的交点的x轴坐标，此时的计算函数其实类似与b中的公式，只需要将x0和这两个上下限，改成由随k而变的，这两个值也可以利用每次二分迭代k的时候，使用二分迭代求得。最终利用b中的积分和船的总体积求得排水体积。

最终那个吃水线方程为。

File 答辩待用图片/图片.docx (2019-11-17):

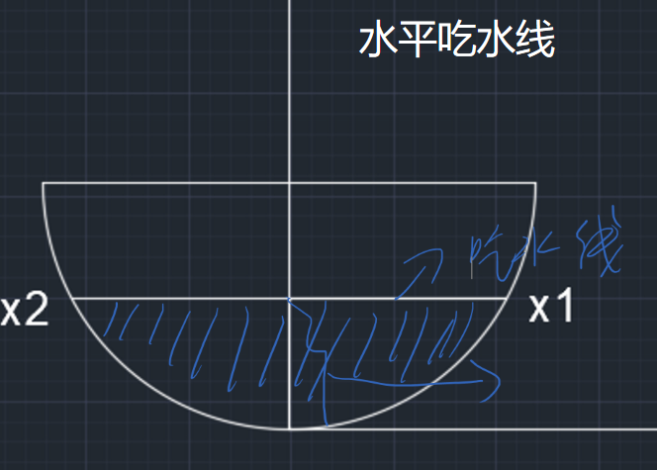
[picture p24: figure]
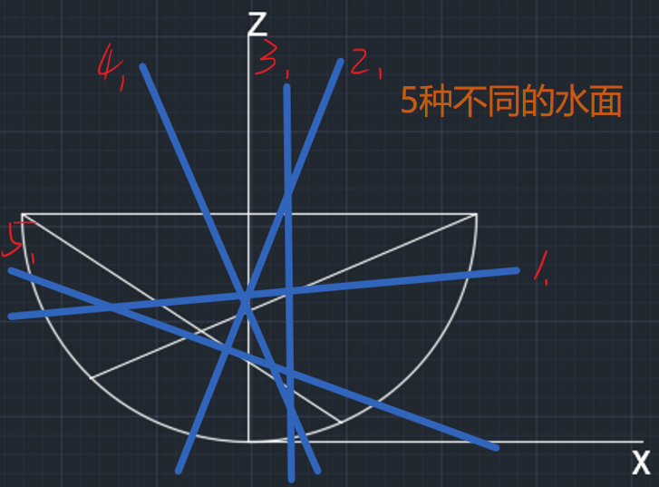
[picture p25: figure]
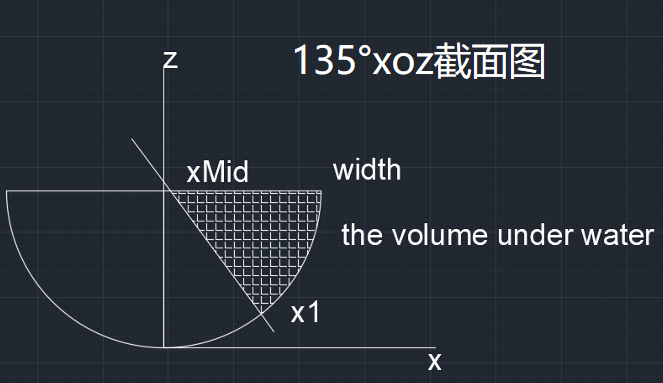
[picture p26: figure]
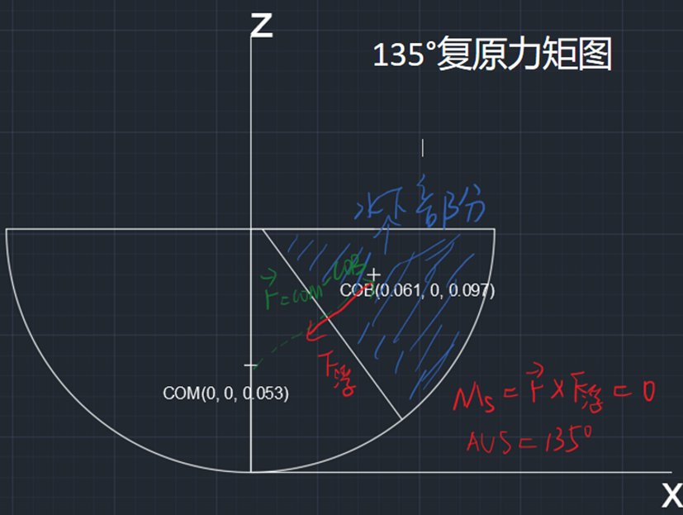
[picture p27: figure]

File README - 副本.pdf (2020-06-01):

# MEAD_PRO_1_Boat-Design


fig 1. 心动号

fig 2. 小船solidwords三维模型图

机器人学院的MEAD 项目--小船项目分享


fig 3. 小船骨架设计cad二维工程图

## 一、MADE项目任务书-- 船只设计项目

Welcome to the MADE project!!! Here, MADE stands for Mathematical Analysis and Design for Engineering. This is a project-based course, which aims at improving the participators’ understanding of mathematics knowledge and engineering analysis. MADE should be able to help the students to develop a thinking mode of applying theoretical analysis and quantitative calculation, and truly understand the role of mathematics in engineering projects.

欢迎来到MADE项目课程。在这里，MADE代表着“用于工程的数学分析和设计”。MADE项目力求以 实际应用的案例加深参与者对数学知识与分析方法的理解，并逐步建立在工程问题中采用理论分析进行 定量计算的思维模式，真正掌握在实际的工程设计中应用数学知识的方法。
MADE course is supposed to be challenging, comprehensive, and integrate knowledge of various subjects. But please be assured that the task is feasible, and we look forward to seeing you confidently say, ”Yes, I MADE it!!”

MADE课程在设计时，就力求做到具有挑战性，全面性，并整合各种科目的知识。但请放心，这项 任务是可行的。我们期待看到你自信地说：“Yes， I MADE it！”

MADE Project 1: Boat Design

此项目要求你设计一艘船，并满足一定的设计要求。要达到这些要求，你必须要完成制作、测试、研究 和计算等多项工作。我们希望通过这项课程中对设计与分析等不同方面的练习，你可以在未来更有信心 的面对各项技术工作。

要完成这个项目，你需要各类工作，制作各类零件，并完成你的设计工作。最后，你要展示你的作品， 并通过答辩。

项目对你的预期：

1. 你应该对船舶设计过程进行背景研究。为此你可能需要在互联网上花费相当多的时间。我们建议你 整理出一个造船业的术语列表，并且要确保自己不仅理解造船业中的why，还要了解其中的how。 这本身是一个巨大的话题。因此，你可能不会成为专家，但应该熟悉关键的思路。你需要理解的术 语包括但不限于：倾斜heel，流线trim，船宽beam，稳定消失角AVS，水下表面积，浮力，位移 等
2. 你应该做一些估算，以指导和验证你更详细的设计和分析工作。任何你做出的决定，你都应该能够 通过一个快速的计算或论证进行支撑。这个计算或论证至少能够表明你的决定在正确的范围内。不 要忘记在正式开始建造你的船模之前检查你的最终设计。设计方案是否准确？它看起来是否稳定？
3. 您应该进行详细的分析以支持您的设计选择，并验证您的测量结果。您应该依靠计算支持你的设计 方案。我们要超越猜测和检查的方式，需要使用图表，研究不同选项等。
4. 你要建造一艘船，并将其性能与你的理论分析预测的性能进行比较。

我们期望你能制造出：

1. 首先，您需要提供一艘船模，并满足下面指定的设计要求。在项目的最后一天，把这艘船带到课堂 上。请注意，在此之前绝对不允许对你的船模进行测试
2. 你需要提供可用于分析给定船舶设计的代码。代码规范细节在文件后续中有说明。
3. 您需要提供一份设计报告，通过计算和测量来对你所做的设计选择进行总结和证明。
4. 最后，您需要提供一份修改后的设计报告以及一封给老师的反馈信，说明在答辩以后，为响应教师 建议所做的修改。

最后要达成的目标

1. 我们将集体做船的测试。想象一个产品展示日
2. 你的团队将与教师一起坐下来审核您的设计报告。教师将为您提供有关如何改进设计报告的具体反 馈等。您将有三天时间修改报告以回应这些建议，并在一页信总结相关的改变。

船只的设计要求

您将使用激光切割的硬质板框架设计和制造船只，并且利用所提供的材料构件外壳。

制造要求

1. 你只能使用一块600mmX450mm的一块硬质板；
2. 必须使用公式驱动的CAD模型创建船只，
3. 船必须接受最小质量为700，最大质量为1000克的货物。在将货物固定在船上之前，应该预先接 受检查和批准。
4. 船必须是不含舭龙骨的单体船设计（即不得使用外延龙骨板或双船体）
5. 船必须包括桅杆。桅杆将是一个0.5米长，直径10mm的铝棒。桅杆的整个长度必须垂直延伸在船 底之上。（不得延伸到船底之外）
6. 应将孔眼按照所需的拖曳点连接到船体上，以便进行速度测试。

性能要求

请记住，在最后一次挑战之前不得进行测试。您应该能够根据计算，知道您的船能否符合以下的各项要 求。

1. 当船满载时，必须能够漂浮起来;
2. 当船满载漂浮时，船的甲板应平行于水面;

3. 满载船的消失稳定角（AVS）应该是135度，允许有±10度误差;
4. 船应具有至少0.2 N-m的最大恢复力矩；
5. 船体应尽可能利于快速行进。这一点将使用拉力测试来确定：通过连接在螺旋孔眼处的水平线施加 0.1牛顿的恒定力来进行。

专业性要求

1. 船模的外观应该很专业；
2. 应该用你们的队名适当装饰你的船模；
3. 制造的船应与报告中的船模设计相同。也就是说，不允许测试前临时修改！！

代码

你要创建一段程序代码，用于计算给定船舶设计的重要参数。本节内容概述了对代码的要求。请注意， 这些要求的编写方式意在引导你逐步增加各项内容。

你的代码应该包含以下内容，

1. 船体形状的数学函数表示。可以使用符号数学或代码来完成，这会创建一组离散的点，来根据函数 形式定义曲面。如果您正在进行二维近似，那么您应该能够在答辩中说明此近似的有效性，包括在 计算中如何考虑第三个维度；
2. 船体形状的可视化，以及来自所有三个方向（纵向，横向和吃水线）的切面的显示
3. 计算给定载荷时的位移，和对于给定载荷和船体倾角的相应吃水线；
4. 为你的船体设计计算质心和浮心，以及这些位置如何随着船体倾角的变化而变化;
5. 在特定负载配置下，你的船体设计方案中，绘制复原力矩作为船体倾斜角函数的曲线图。你应该检 查这些结果，确保它们与计算出的质心和浮心位置保持互相吻合。

## 二、我完成了什么

根据小船设计要求（见小船设计项目任务书文件）

1、求出小船底部曲面方程及船高

2、求出龙骨方程、截面方程及甲板方程

3、求出重心及小船向x轴倾斜135°（船体封闭）时的浮心及复原力矩

4、求出吃水线

5、画数量关系图

5.1画出重物质量与吃水线关系的曲线图

5.2画出船长、宽、高分别与复原力矩关系的曲线图

5.3 画出重物质量与重心关系的曲线图（曲线图的纵横坐标表示重心坐标，曲线上的点的大小表示质 量）

## 三、解决方案概要

针对如何使用一块600mm x500mm的木板制造一艘在承载一定质量的重物的情况下能够平 稳的漂浮起来切具有稳定消失角(AVS)的方案进行了研究。通过数学曲面公式来简单的表示船体的 曲面，通过曲面积分来计算船体体积、吃水线性、船体的浮心和重心，确定浮心、重心之后计算 出倾斜一定角度时的复原力矩。通过使倾斜一定角度时船体重心在浮力方向和船体中心线的交点

## 四、详细解答过程请看项目报告书，找不到自己想要的请留言（by a

## new issue)

图3 船体倾斜135°复原力矩图; RESULT; 复原力臂; 复原力矩; 4.吃水线

上来确定AVS(135°)。
以小船最低点为坐标原点，垂直垂直向上为Z轴，船头至船尾的连线为Y轴建立直角坐标系以方
程为船体底部曲面方程，最终确定A=8.33，B=3.33，计算得船长length为0.379m，宽width为
0.240m高height为0.120m，桅杆重心(0,0,0.292)，重物重心(0,0,0.042)，船体重心为

图4 水平吃水线; 已知船体总重量为; 吃水线方程为; 排 5.关系图


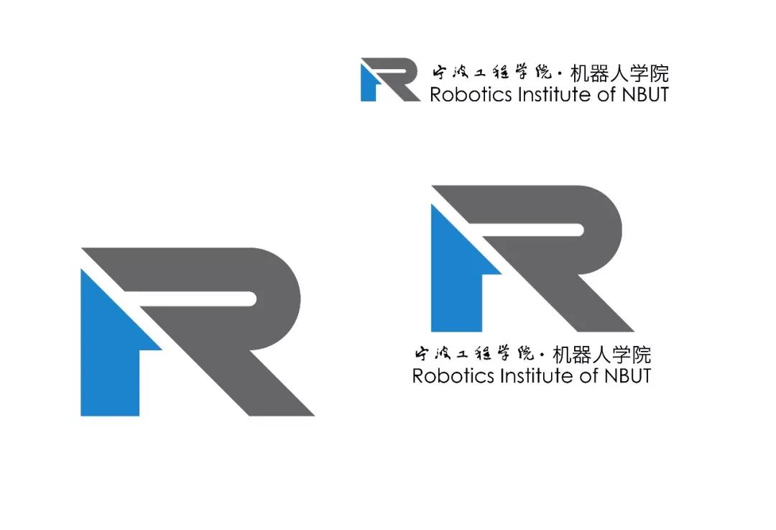
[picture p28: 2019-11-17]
机器人学院图标.jpg

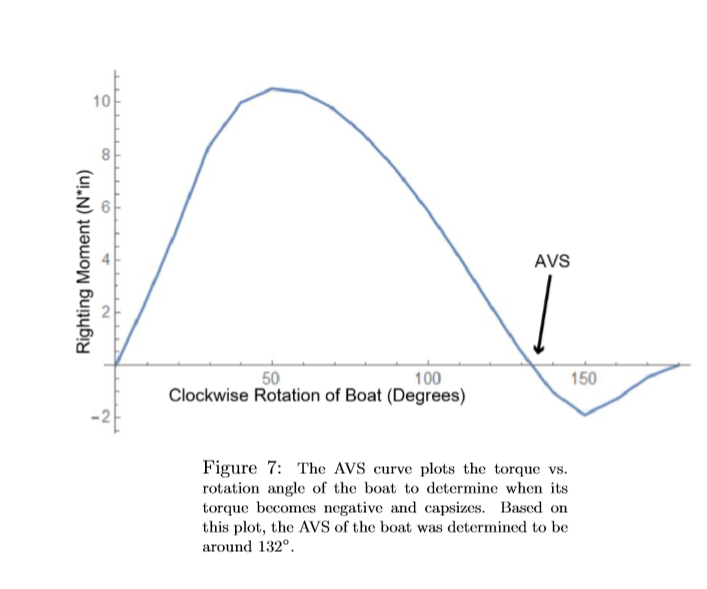
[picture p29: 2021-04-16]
资料/AVS.png

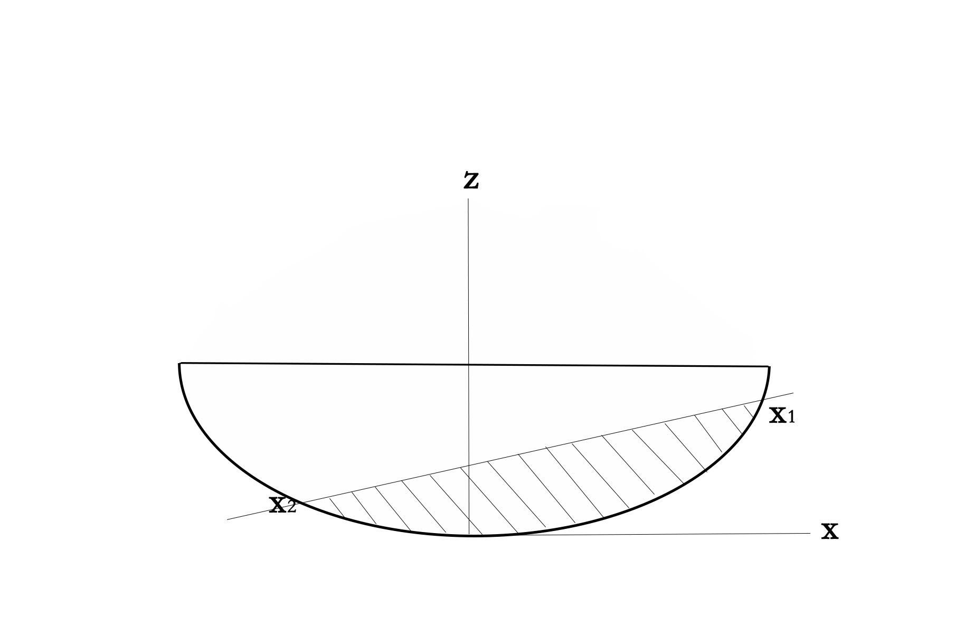
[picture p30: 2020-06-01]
答辩待用图片/0-theta_r水面与船体xoz平面图.jpg

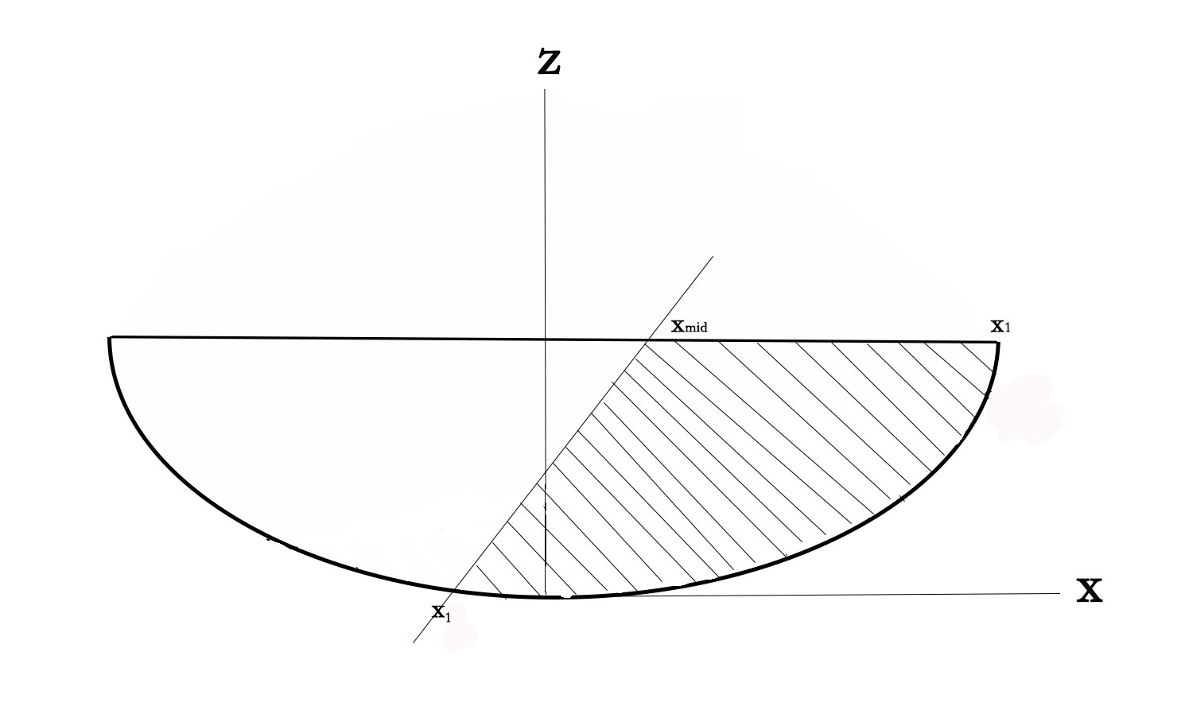
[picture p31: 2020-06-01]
答辩待用图片/theta_R--pi_2时水面与船体xoz平面图.jpg

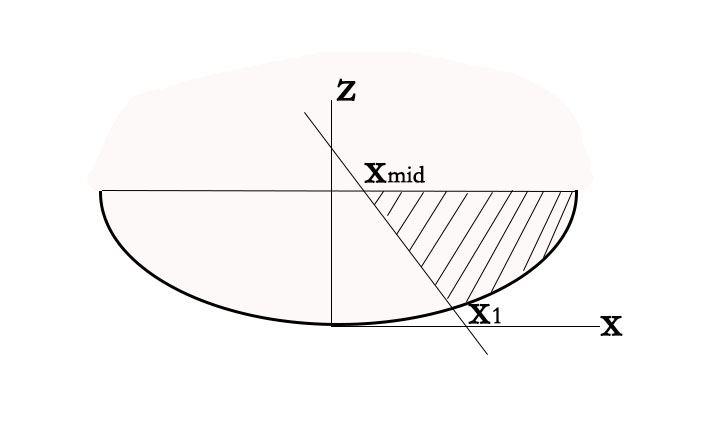
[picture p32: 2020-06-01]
答辩待用图片/pi_2--theta_L.jpg

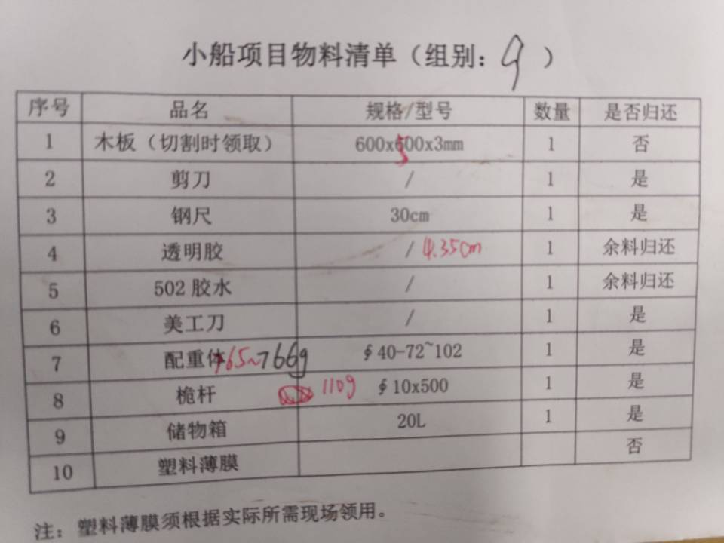
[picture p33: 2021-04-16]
资料/材料信息.jpg

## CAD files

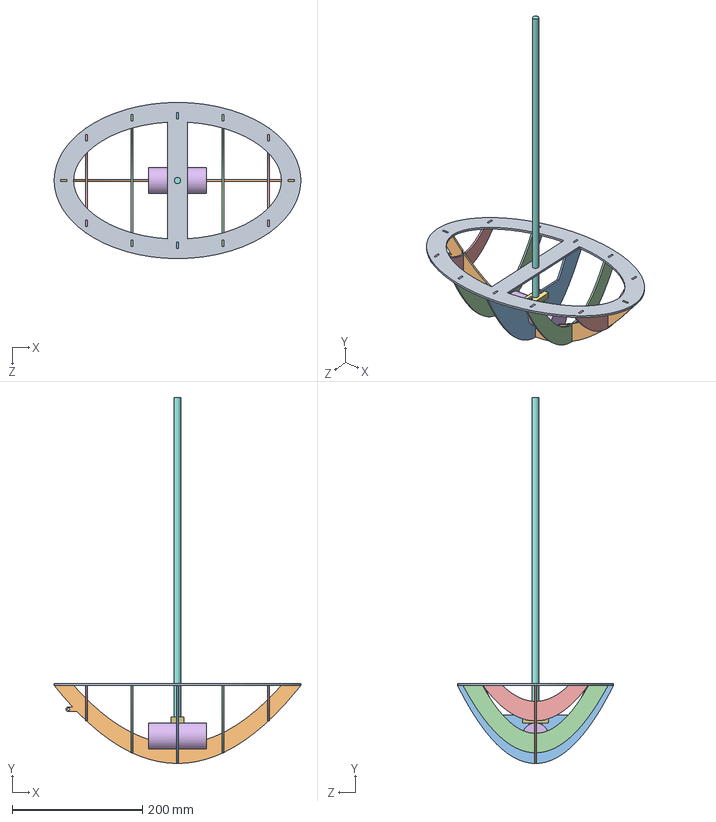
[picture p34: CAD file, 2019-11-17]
小船信息/小船3d模型-solidworks/装配体1.SLDASM
379.0 x 562.4 x 240.0 mm
甲板
龙骨
中间肋骨
肋骨1 x 2
肋骨2 x 2
铁块
垫片 x 3
零件6

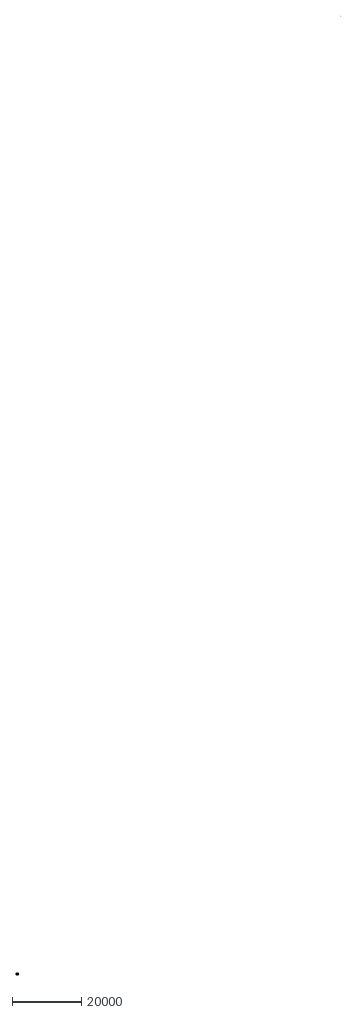
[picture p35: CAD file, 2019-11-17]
小船信息/44(9组-曹鹏霄-张凯科）.dxf
94015.5 x 277714.7

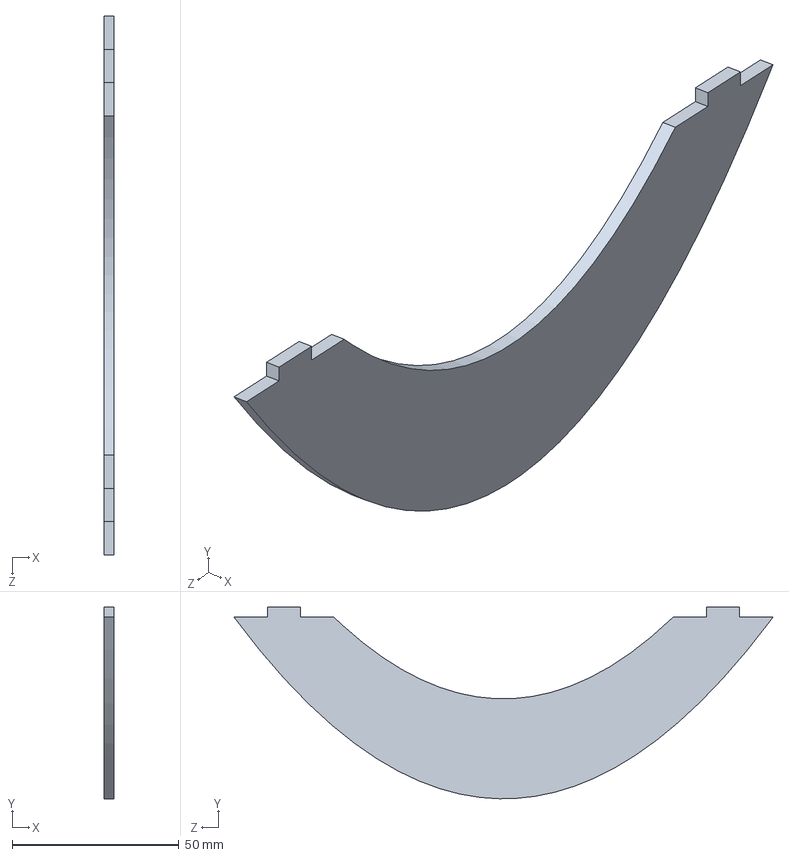
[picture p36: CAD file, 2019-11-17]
小船信息/小船3d模型-solidworks/肋骨2.SLDPRT
3.00 x 57.5 x 161.7 mm

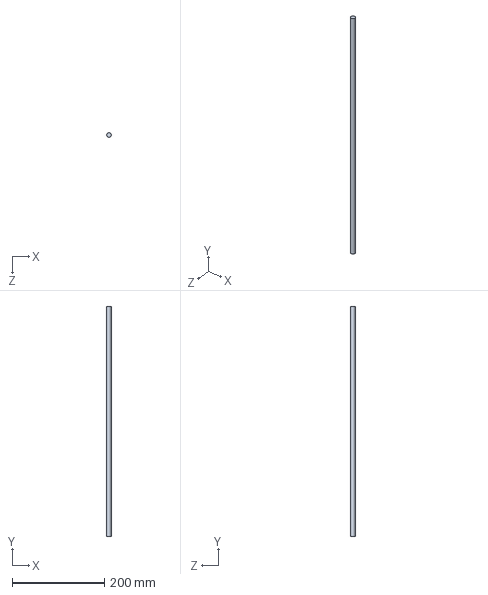
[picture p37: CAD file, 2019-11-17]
小船信息/小船3d模型-solidworks/零件6.SLDPRT
10.0 x 500.0 x 10.0 mm

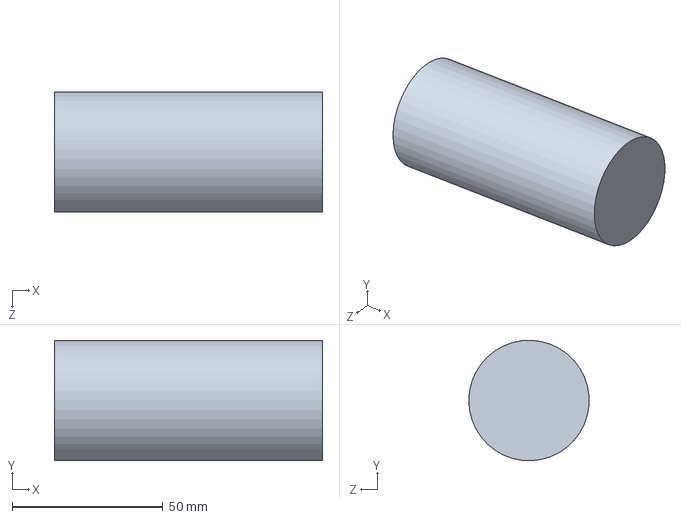
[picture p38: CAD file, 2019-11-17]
小船信息/小船3d模型-solidworks/铁块.SLDPRT
89.0 x 40.0 x 40.0 mm

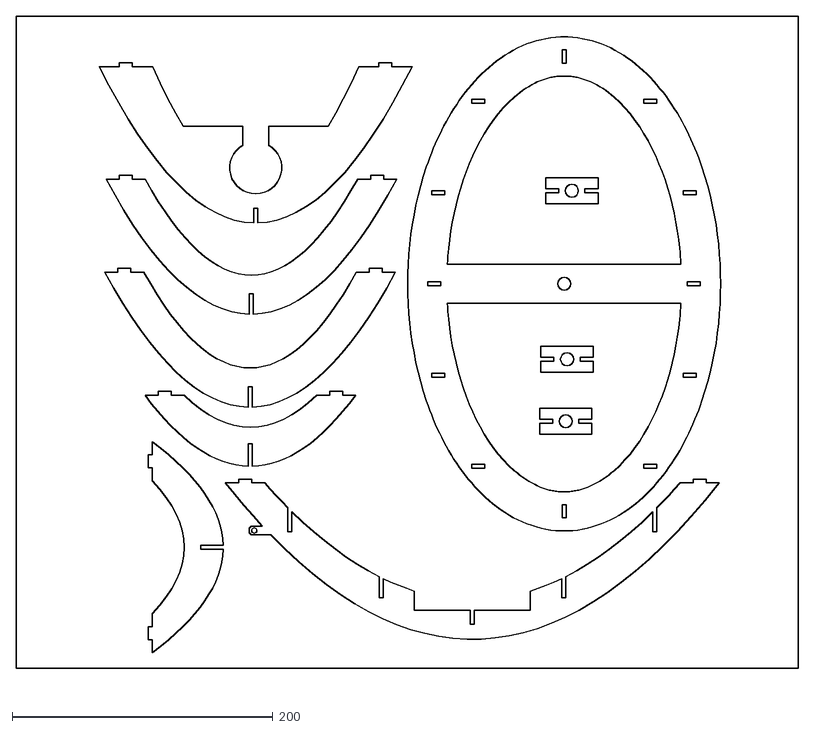
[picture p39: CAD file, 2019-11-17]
小船信息/小船3d模型-solidworks/07.dxf
600.0 x 516.5

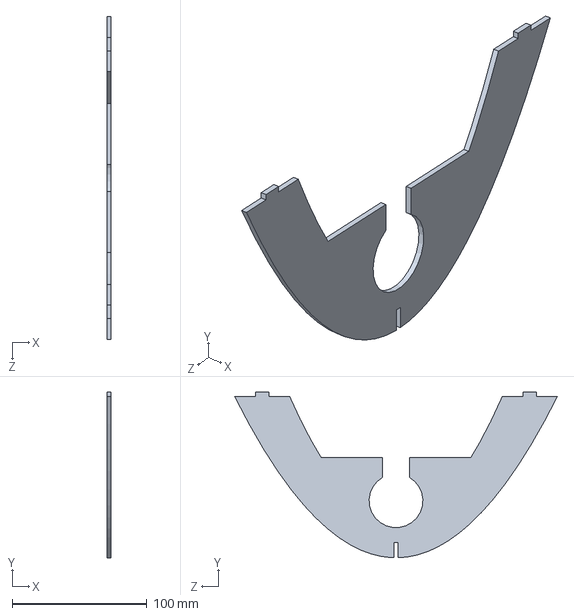
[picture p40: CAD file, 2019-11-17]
小船信息/小船3d模型-solidworks/中间肋骨.SLDPRT
3.00 x 123.0 x 240.0 mm

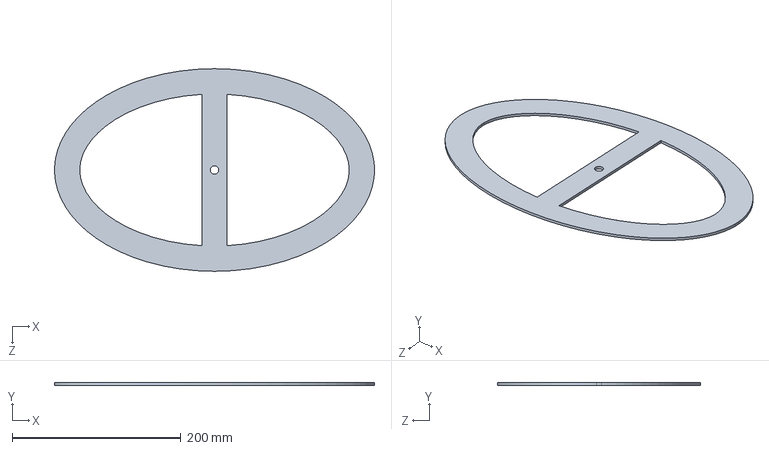
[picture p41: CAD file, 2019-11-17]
小船信息/小船3d模型-solidworks/甲板.SLDPRT
379.0 x 3.00 x 240.0 mm

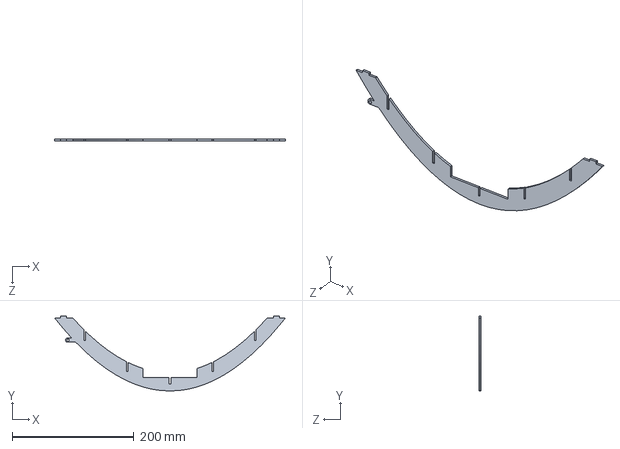
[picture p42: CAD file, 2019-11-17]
小船信息/小船3d模型-solidworks/龙骨.SLDPRT
379.0 x 122.9 x 3.00 mm

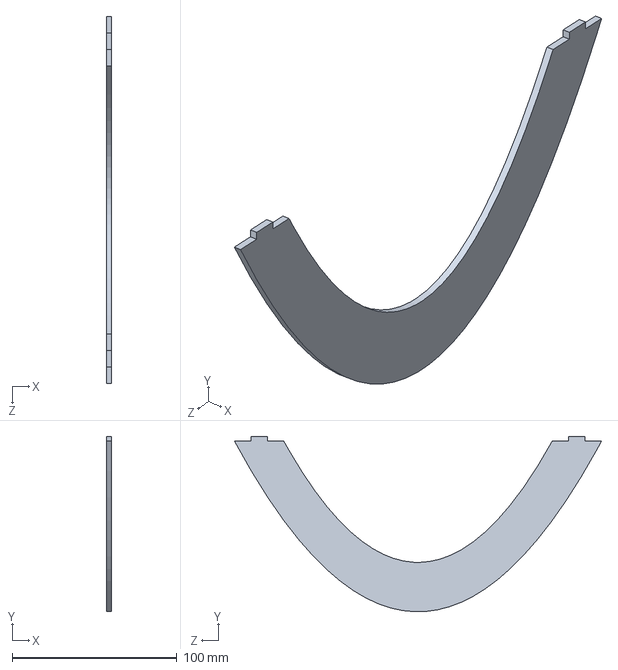
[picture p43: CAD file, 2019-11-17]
小船信息/小船3d模型-solidworks/肋骨1.SLDPRT
3.00 x 106.6 x 223.0 mm

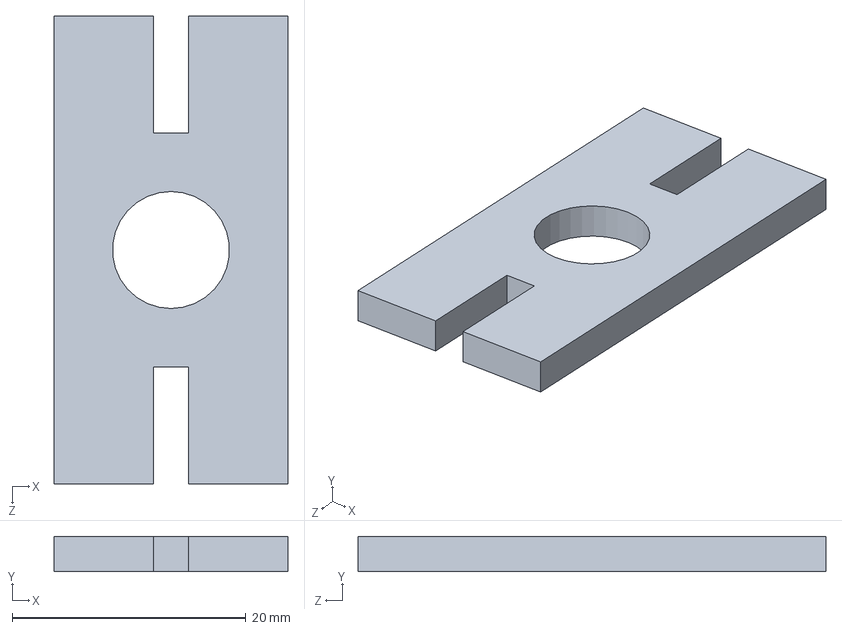
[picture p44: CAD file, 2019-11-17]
小船信息/小船3d模型-solidworks/垫片.SLDPRT
20.0 x 3.00 x 40.0 mm

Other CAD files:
小船信息/小船-心动号.STL
小船信息/07甲板填充后.dwg
小船信息/waterLine.dwg
小船信息/小船3d模型-solidworks/裁剪图.dwg
小船信息/小船3d模型-solidworks/中间肋骨.DWG
小船信息/小船3d模型-solidworks/垫片.DWG
小船信息/小船3d模型-solidworks/甲板.DWG
小船信息/小船3d模型-solidworks/肋骨1.DWG
小船信息/小船3d模型-solidworks/肋骨2.DWG
小船信息/小船3d模型-solidworks/龙骨.DWG

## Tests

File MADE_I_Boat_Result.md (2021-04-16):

# Result

### 1.1曲面方程

$$
Ax^2+By^2=z
$$

### 1.2船高

$$
H
$$

### 2.1龙骨方程

$$
By^2=H
$$

### 2.2截面方程

#### 	2.2.1 xoz平面

$$
\{{Ax^2=z \atop y=0}
$$

#### 	2.2.1 xoz平面

$$
\{{By^2=z \atop x=0}
$$

### 2.3甲板方程

$$
Ax^2+By^2=H
$$

### 3.1重心

<center>表1 船体各部件符号表示</center>
| | 字母下标 | 质量/kg | 规格/型号 单位/m | 重心/m |
| ---- | --- | --- | --- | --- |
| 桅杆 | a | 0.110 | $ \phi0.010\times0.500$ | (0, 0, 0.312) |
| 船体 | b | 0.321 | $0.379\times0.240\times0.120$ | (0, 0, 0.080) |
| 重物 | c | 0.770 | $\phi0.020\times0.078$ | (0, 0, 0.042) |
| 整体 | all | 1.201 | $0.379\times0.240\times0.120$ | (0, 0, 0.053) |

已知桅杆重心为$COM_a(0,0,z_{M_a})$，船体重心为$COM_b(0,0,z_{M_b})$，重物重心为$COM_c(0,0,z_{M_c})$

则整体重心为$COM_c(0,0,z_{M_{all}})$
$$
z_{M_{all}}=\frac{m_a\times z_{M_a}+m_b\times z_{M_b}+m_c\times z_{M_c}}{m_a+mb+mc}\tag{1}
$$

### 3.2倾斜135°时的浮心



<center>图1 船体倾斜135°时水面方程图三维视图


<center>图2 船体倾斜135°时水面方程图xoz截面图

浮心计算$(x_b, y_b, z_b)$

已知水面方程为$z=px+z_0$，其中 $p=tan\theta$，$\theta=135°$，$z_0=\sqrt{\frac{H-Ax^2}{B}}$

有
$$
\begin{align}
x_b=&\frac{2}{V}\iiint_E{xdV}\qquad E = \{(x,\ y, \ z) | x_{Mid}\leq x\leq width, \ y_0\leq y \leq0, 0 \leq z \leq z_0 \}\tag{2}\\

x_b=&\int_{xMid}^{x_1}\int_{0}^{y_0}\int_{px+z_0}^{H}{xdzdydx}\tag{3}
\end{align}
$$
计算得浮心$COB=(0.061, 0, 0.097)$

### 3.3复原力矩



<center>图3 船体倾斜135°复原力矩图

已知$COM(0,0,z_m)$，$COB(x_b,0,z_b)$

浮力$F_浮=<tan\theta,0,-1>\lambda$，其中$\lambda=\frac{G_{all}}{tan^2\theta+1}$

复原力臂$r=COM-COB=<0,0,z_m-z_b>$

复原力矩$M_s=r\times F_浮=0$

### 4.吃水线



<center>图4 水平吃水线

已知船体总重量为$m_{all}$，有$m_{all}=\rho g_水 v_排$

吃水线方程为$z=h$

有
$$
\begin{align}v_排=&\iiint_E{dV}\qquad E = \{(x,\ y, \ z) | x_{Mid}\leq x\leq width, \ y_0\leq y \leq0, 0 \leq z \leq z_0 \}\tag{4}\\v_排=&\int_{xMid}^{x_1}\int_{0}^{y_0}\int_{Ax^2+Bx^2}^{h}{xdzdydx}\tag{5}\end{align}
$$

### 5.数量关系图

### 5.1重物与吃水线

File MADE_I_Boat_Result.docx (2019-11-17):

# 1.1 曲面方程

  1.2 船高
  2.1 龙骨方程
  2.2 截面方程

2.2.1 xoz平面

2.2.1 xoz平面

2.3甲板方程

  3.1 重心

表1 船体各部件符号表示

| 字母下标 | 质量/kg | 规格/型号 单位/m | 重心/m
桅杆 | a | 0.110 | | (0, 0, 0.312)
船体 | b | 0.321 | | (0, 0, 0.080)
重物 | c | 0.770 | | (0, 0, 0.042)
整体 | all | 1.201 | | (0, 0, 0.053)

已知桅杆重心为 ，船体重心为 ，重物重心为 则整体重心为

# 3.2 倾斜135°时的浮心

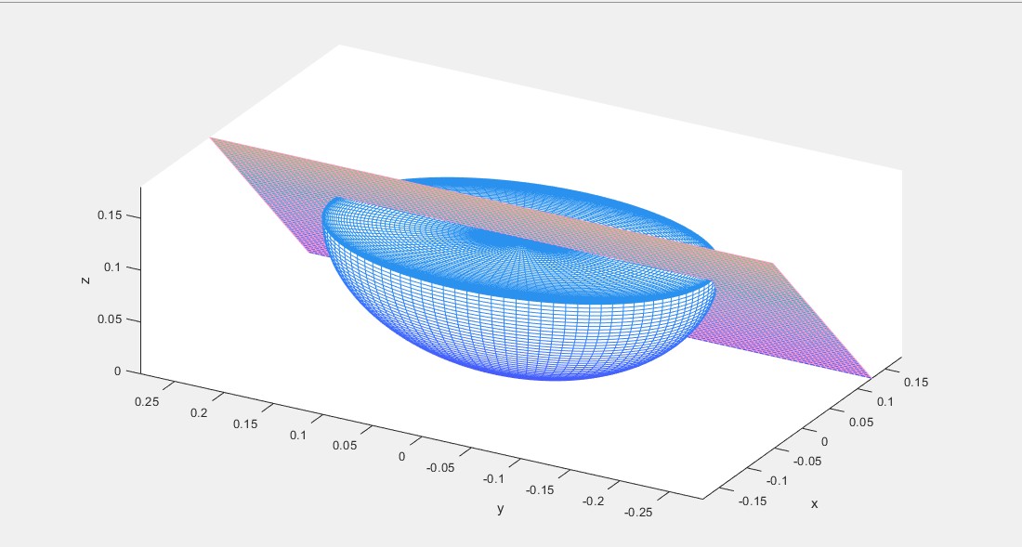
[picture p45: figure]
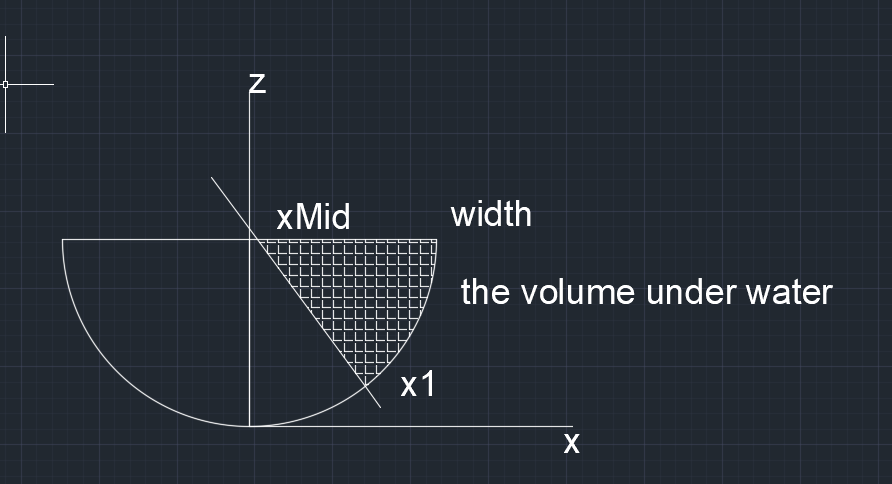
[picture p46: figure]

图1 船体倾斜135°时水面方程图三维视图

图2 船体倾斜135°时水面方程图xoz截面图

浮心计算

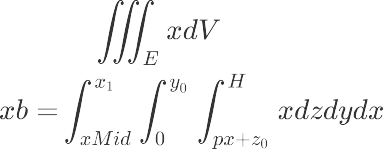
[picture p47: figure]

已知水面方程为 ，其中 ， 有

计算得浮心

# 3.3 复原力矩

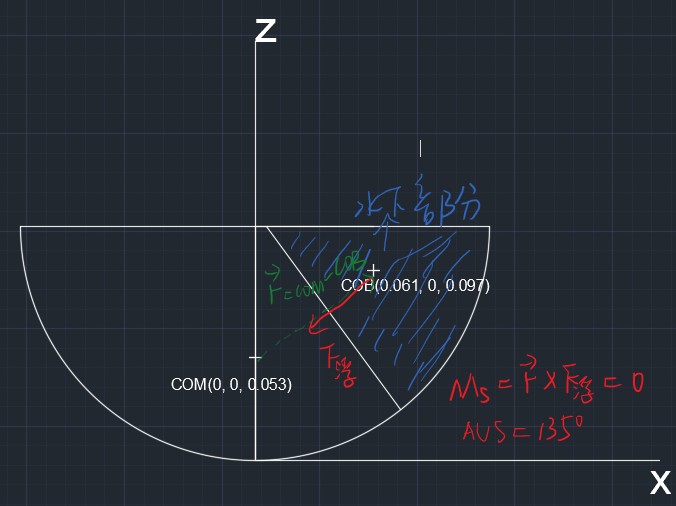
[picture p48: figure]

图3 船体倾斜135°复原力矩图

已知 ，

浮力 浮 ，其中

复原力臂

复原力矩 浮

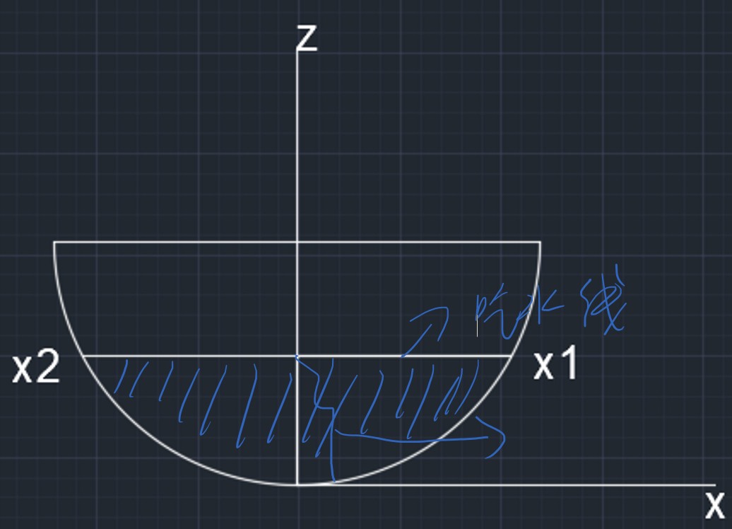
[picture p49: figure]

# 4. 吃水线

图4 水平吃水线

已知船体总重量为 ，有 水 排

吃水线方程为有

排 排

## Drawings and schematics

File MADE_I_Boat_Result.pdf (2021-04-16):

# Result

## 1.1曲面方程

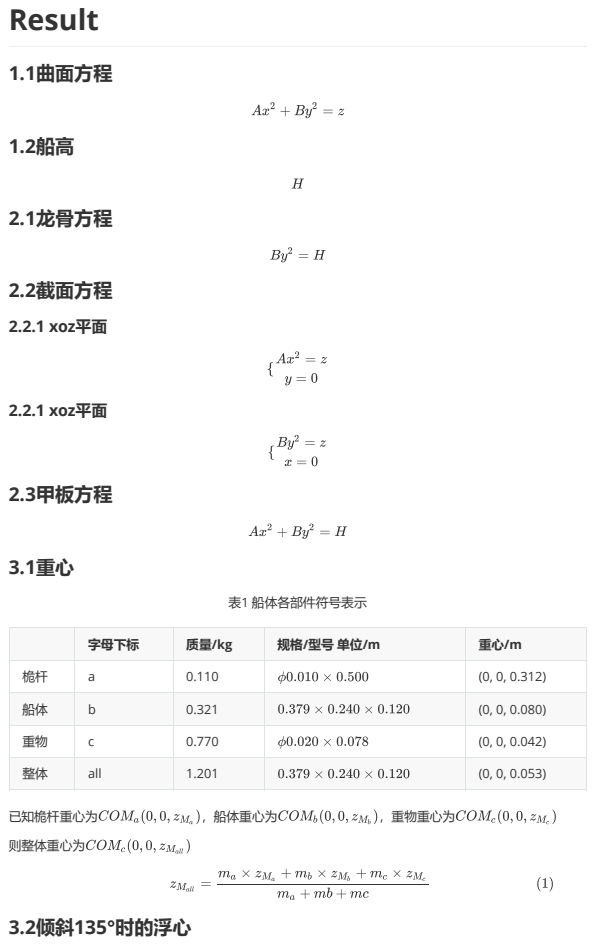
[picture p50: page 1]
表1 船体各部件符号表示; 2.1龙骨方程; 2.2截面方程; 2.2.1 xoz平面; 2.3甲板方程; 已知桅杆重心为; ，船体重心为; ，重物重心为; 则整体重心为; 3.2倾斜135°时的浮心

字母下标 | 质量/kg | 规格/型号 单位/m | 重心/m

整体 | all | 1.201 | | (0, 0, 0.053)

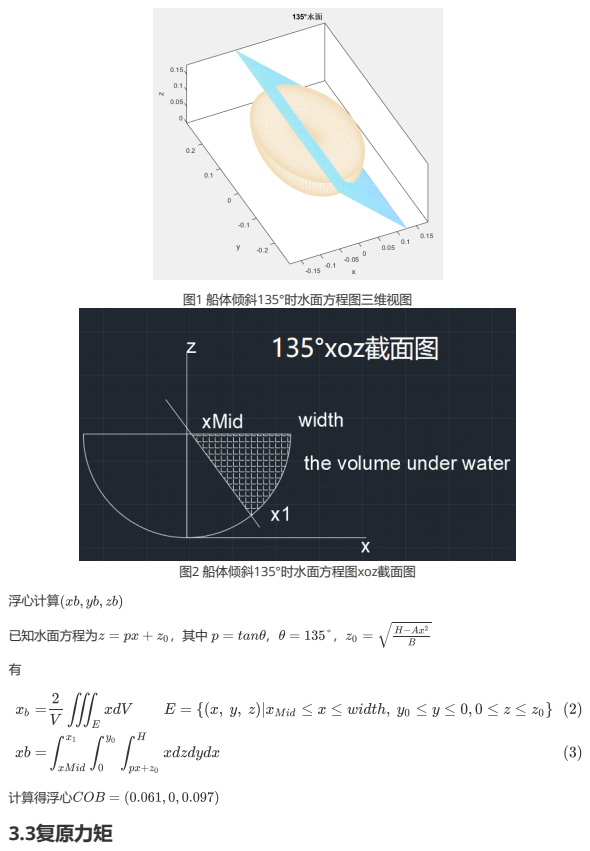
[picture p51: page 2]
图1 船体倾斜135°时水面方程图三维视图; 图2 船体倾斜135°时水面方程图xoz截面图; 浮心计算; 已知水面方程为; 计算得浮心 3.3复原力矩

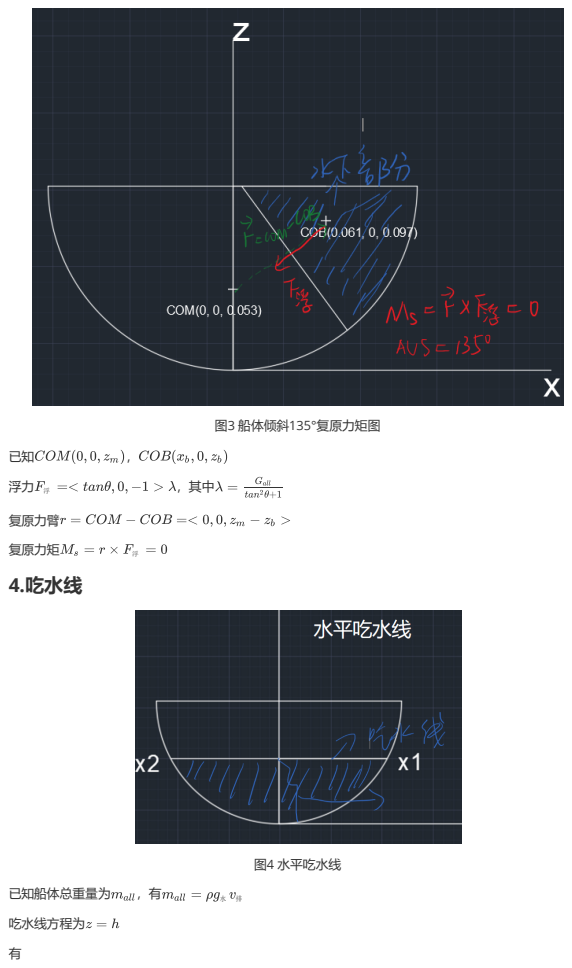
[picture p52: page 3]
图3 船体倾斜135°复原力矩图; 图4 水平吃水线; 复原力臂; 复原力矩; 4.吃水线; 已知船体总重量为; 吃水线方程为

## 5.数量关系图 5.1重物与吃水线

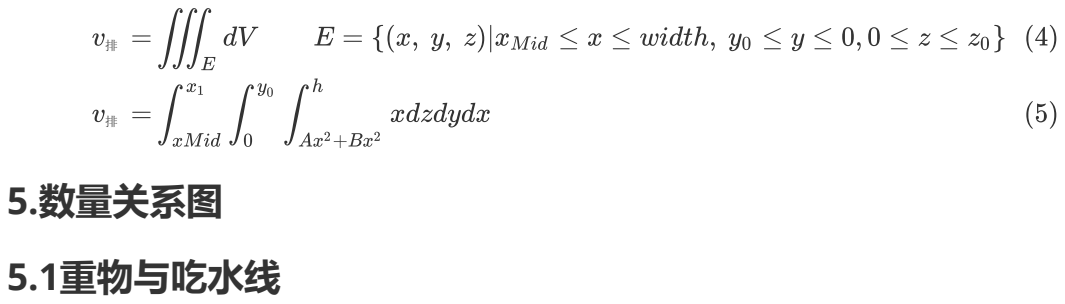
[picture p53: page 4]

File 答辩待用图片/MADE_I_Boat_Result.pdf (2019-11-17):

# Result

## 1.1曲面方程

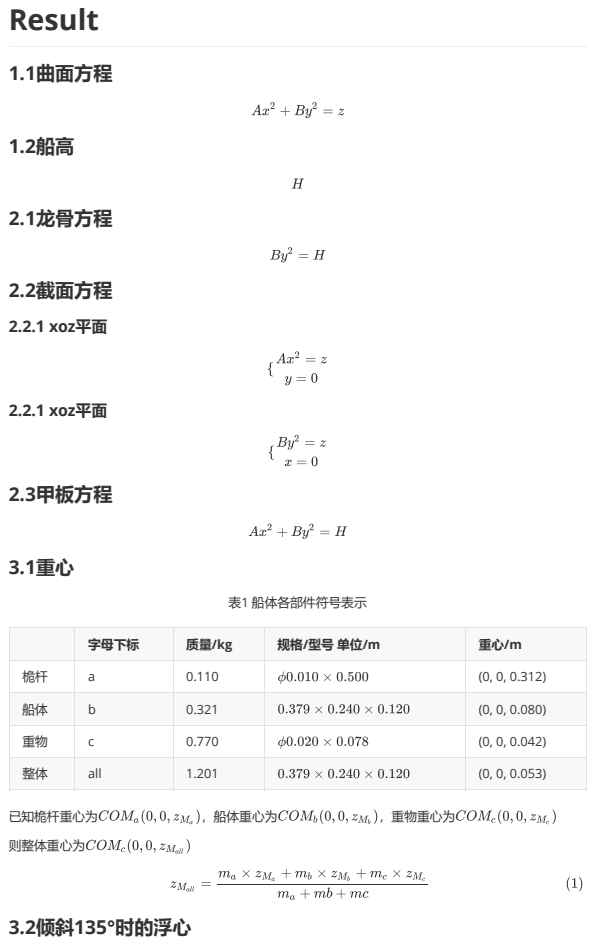
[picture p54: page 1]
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

字母下标 | 质量/kg | 规格/型号 单位/m | 重心/m

整体 | all | 1.201 | | (0, 0, 0.053)

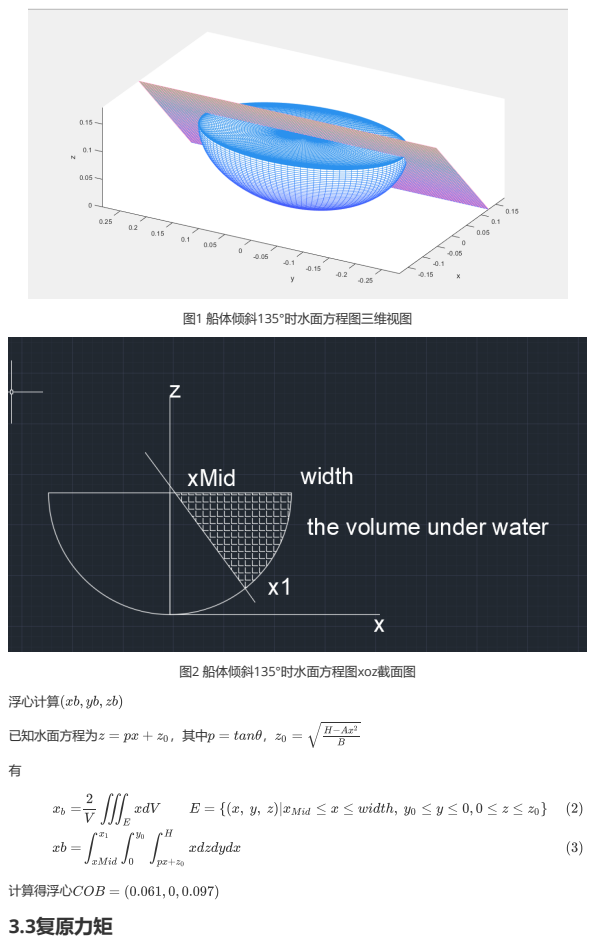
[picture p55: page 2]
图1 船体倾斜135°时水面方程图三维视图; 图2 船体倾斜135°时水面方程图xoz截面图; 浮心计算; 已知水面方程为; 计算得浮心 3.3复原力矩

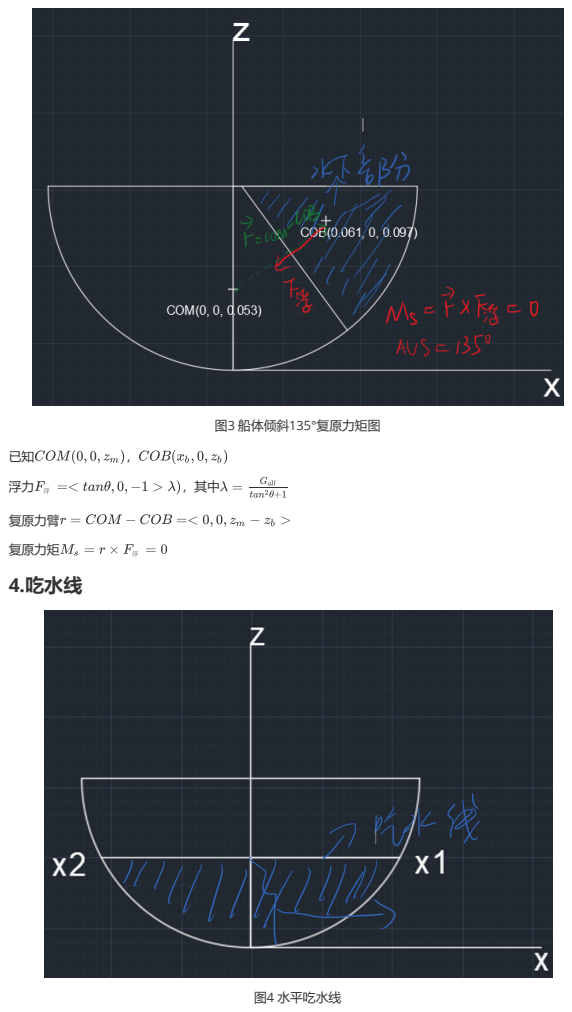
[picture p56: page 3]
图3 船体倾斜135°复原力矩图; 图4 水平吃水线; 复原力臂; 复原力矩; 4.吃水线

## 5.数量关系图 5.1重物与吃水线

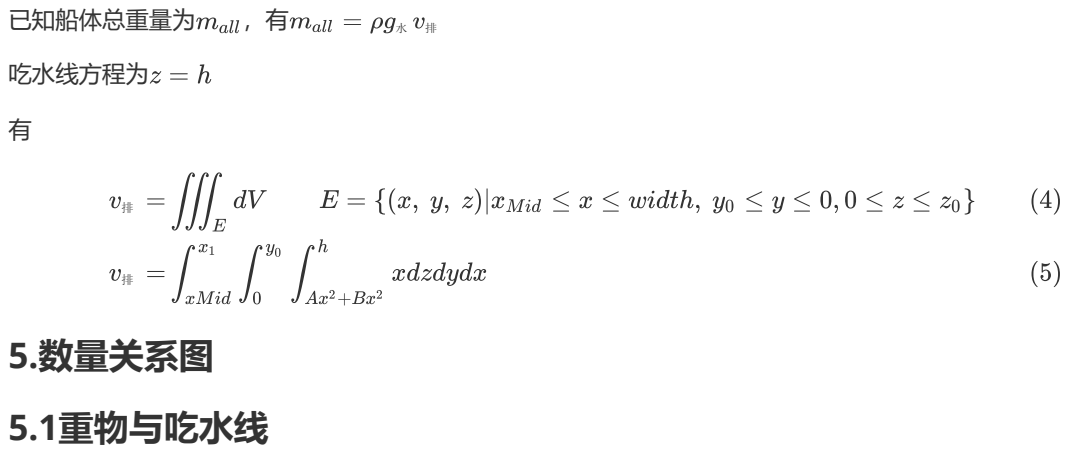
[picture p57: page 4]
已知船体总重量为; 吃水线方程为

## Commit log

2019-10-05 update the matlab doc
    [promble_1.xlsx]
2019-11-17 小船项目完结，更新所有计算代码，图片，项目报告
    [07.dxf, 07甲板填充后.dwg, 44(9组-曹鹏霄-张凯科）.dxf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]
2020-06-01 更新READMEE
    [小船-心动号.STL]
